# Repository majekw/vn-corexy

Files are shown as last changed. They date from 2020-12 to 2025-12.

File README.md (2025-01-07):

# vn-corexy
Very Narrow CoreXY 3D Printer

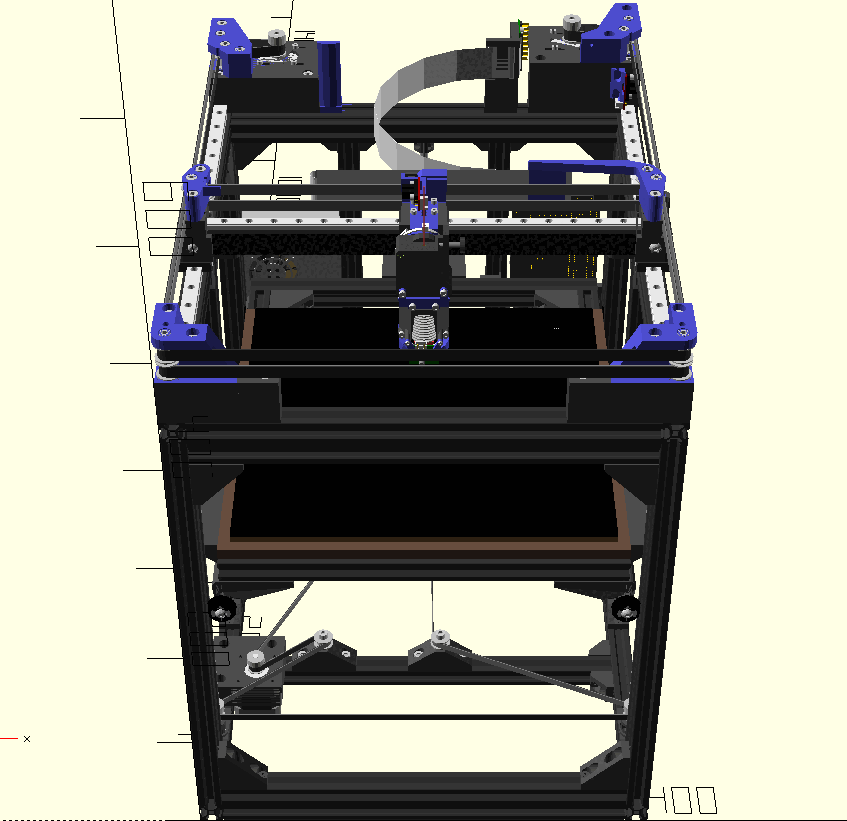
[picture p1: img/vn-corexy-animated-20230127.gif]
vn-corexy rendering


vn-corexy is designed around 300x300 mm build plate with goal to be
as compact as possible with focus on width. Current dimensions are
390(width)x520(depth)x520(height) mm. Only filament could stick above
maximum height, everything else (including cables) are within size limits.

In this repository there is OpenScad source code with 3D printer design.
There are many parameters that can be customized. In Customizer you could
choose which printed parts you want to render and save as STL file.
There are also ECHO messages in console that can be used to prepare BOM,
for example there are messages with all lengths of specific extrusion types,
GT2 belt lengts are also calculated.

**WARNING: While this is almost finished, THIS IS STILL WORK IN PROGRESS**

Forum thread (in Polish): https://reprapy.pl/viewtopic.php?f=10&t=7225

YouTube videos: https://youtube.com/playlist?list=PL_tFeFf-6be2vM2YfxNyLlgO5D3nhVPHG

# Requirements
- OpenScad https://www.openscad.org/
- NopSCADlib library https://github.com/nophead/NopSCADlib (version 21.32.0)
- for Sailfin extruder checkout Sailfin-Extruder/ git submodule
- for Moli extruder checkout Moli-Extruder/ git submodule
- for MRF extruder, download stl files from https://www.thingiverse.com/thing:5149028
  and put them into MRF/ directory

# Supported configuration
Extruders:
- TBG-Lite
- HGX Lite 2.0
Hotend:
- CHC heating block
Bed probes:
- Mini differential IR probe
- BL-Touch
Bed stabilization:
- v-slot wheels

# Known issues
- MGN12 carriage sticks 3.5mm out of frame
- bed frame could be 10mm shorter to use 4 the same wheel supports
- bed frame wheels supports are temporary, will be changed in future (work
  in progress on on MGN7 rails)
- Sailfin, Moli and MRF extruders support is not finished, BMG extruder
  is abandoned.

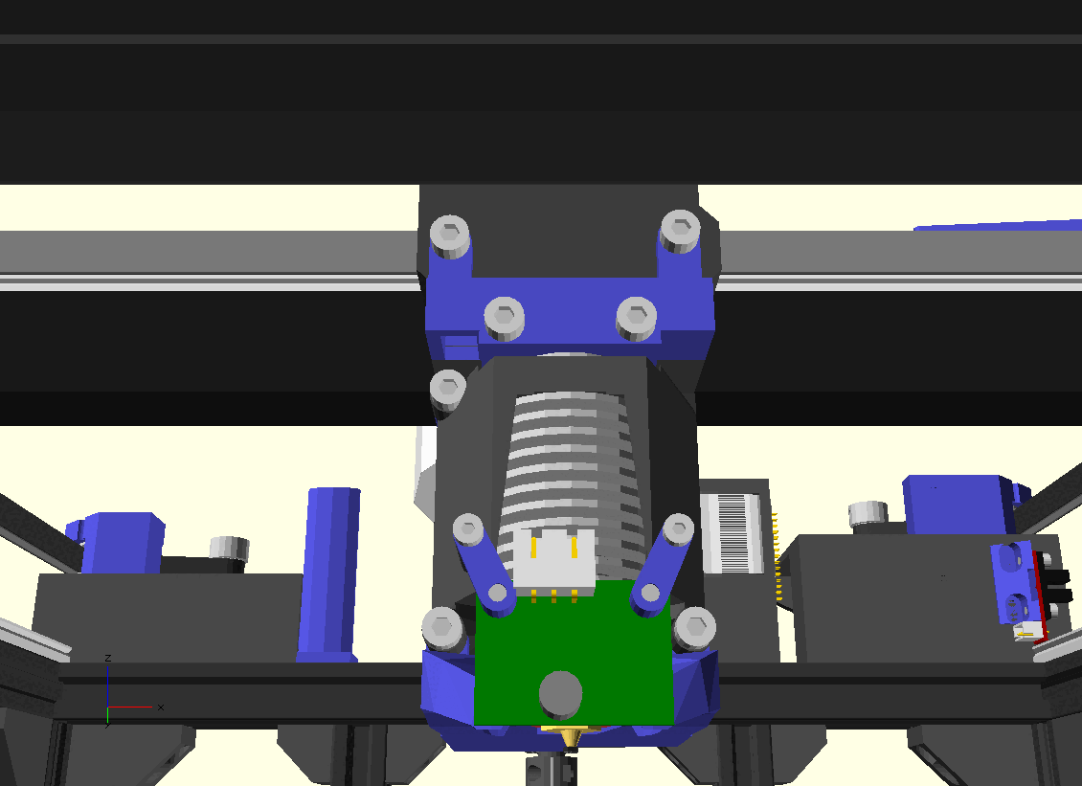
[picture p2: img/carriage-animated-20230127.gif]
vn-corexy carriage rendering


# Copyright & license
(C) 2020-2024 Marek Wodzinski <majek@w7i.pl>

This work is licensed under Creative Commons Attribution-ShareAlike 4.0 International License.
You should have received a copy of the license along with this work. 
If not, see http://creativecommons.org/licenses/by-sa/4.0/

BL-Touch model (STL) by @EA3D from: https://www.printables.com/model/301723-bltouch 
is under a Creative Commons (International License) Public Domain

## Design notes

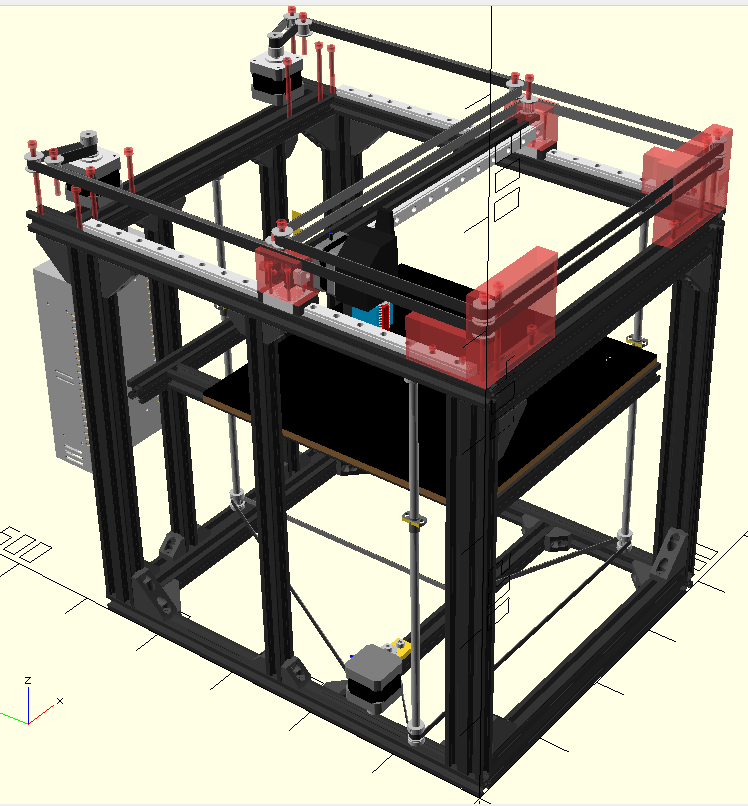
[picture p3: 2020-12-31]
img/vn-corexy-20201230.png

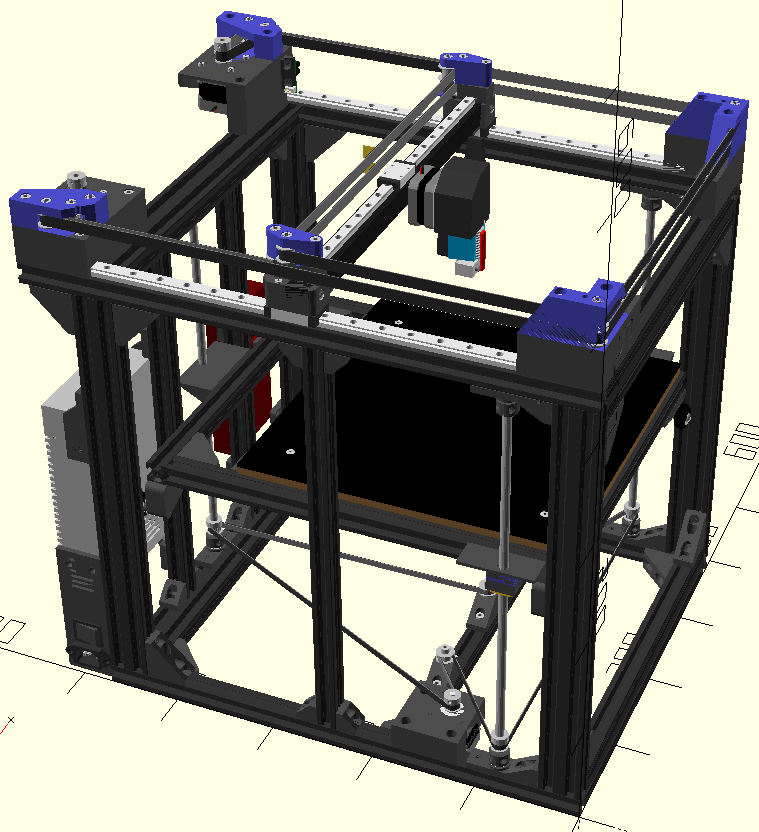
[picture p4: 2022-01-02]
img/vn-corexy-20220103.png

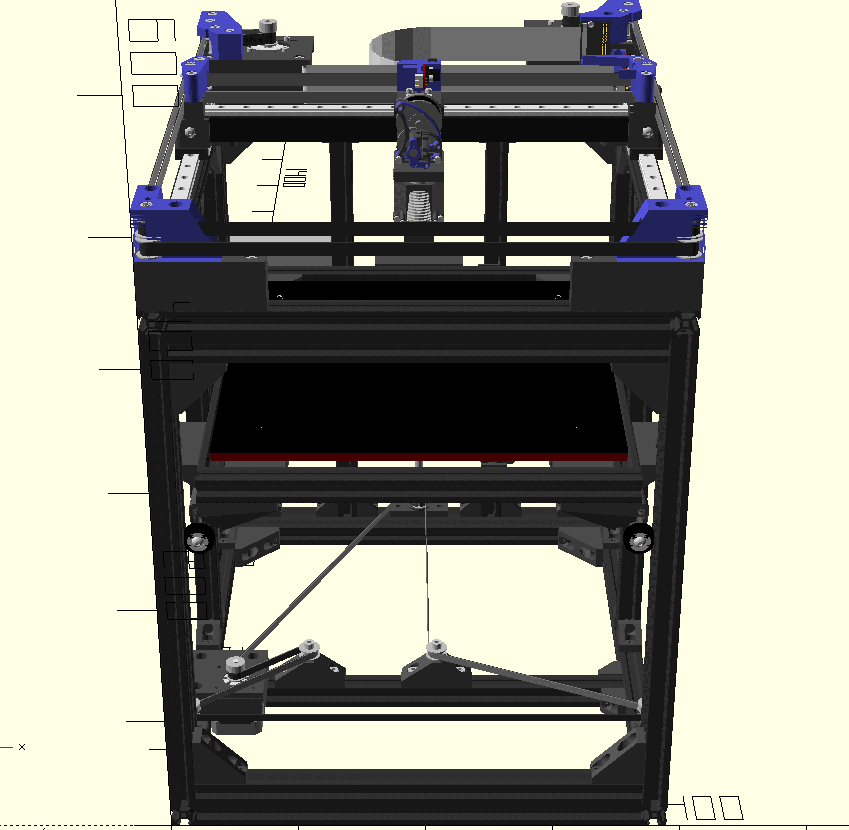
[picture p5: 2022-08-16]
img/vn-corexy-animated-20220816.gif

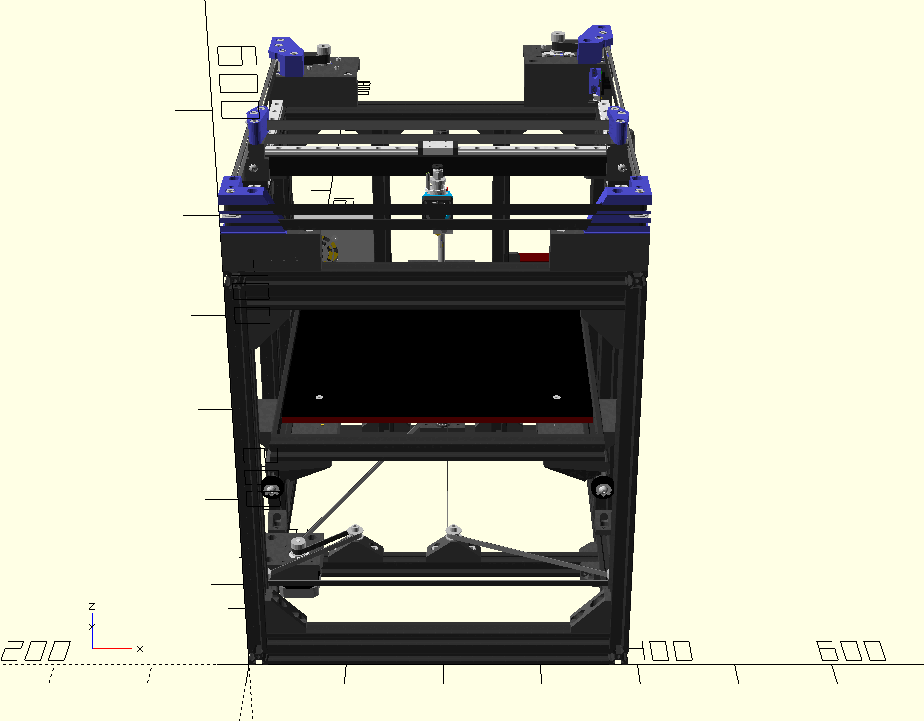
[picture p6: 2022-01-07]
img/vn-corexy-animated-20220105.gif

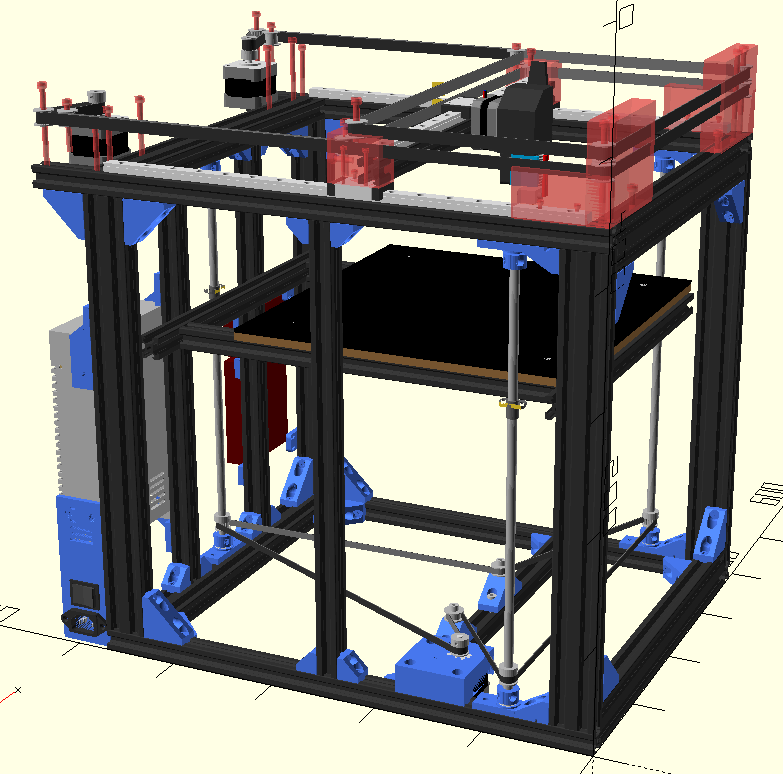
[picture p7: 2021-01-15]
img/vn-corexy-20210115.png

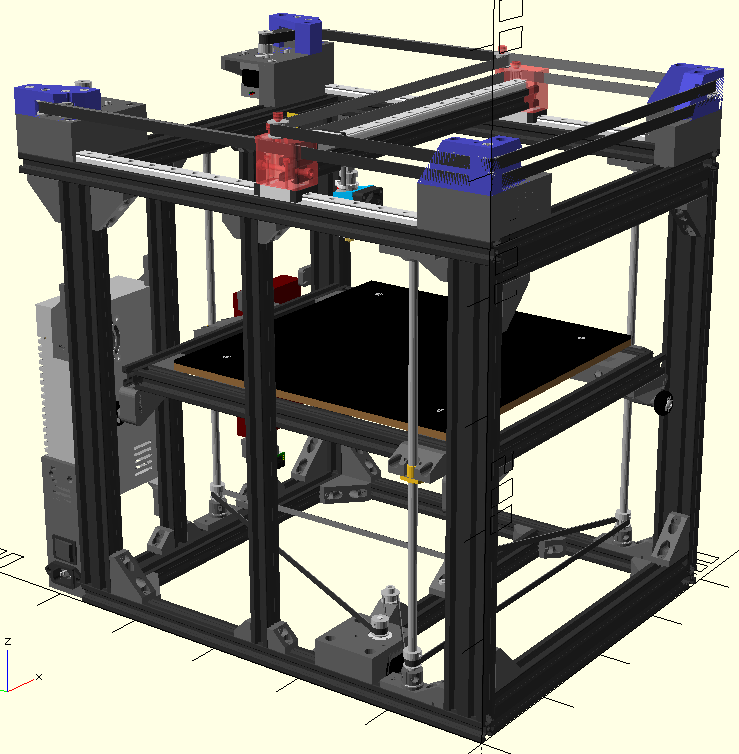
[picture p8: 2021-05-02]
img/vn-corexy-20210502.png

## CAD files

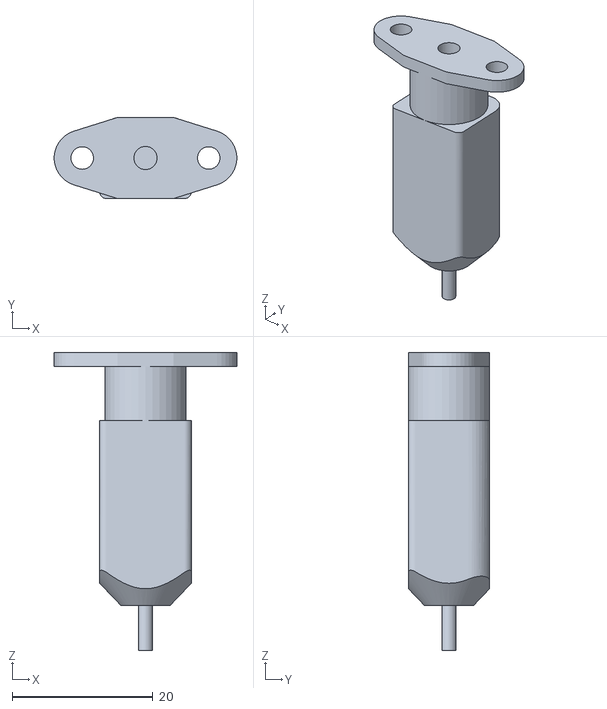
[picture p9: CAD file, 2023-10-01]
BL-touch.stl
26.0 x 11.6 x 42.4

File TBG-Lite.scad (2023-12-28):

/*
  TBG-Lite extruder OpenSCAD library
  
  Based on datasheet and measures of TBG-Lite_mockup.STEP
  (C) 2022 Marek Wodzinski <majek@w7i.pl>
  
  This library is licensed under a Creative Commons Attribution-ShareAlike 4.0 International License.
  You should have received a copy of the license along with this work.
  If not, see <http://creativecommons.org/licenses/by-sa/4.0/
  
  Some basic dimensions:
  - holes for screws: 3.2mm, head 5.5mm
  - corners: 2.5mm from edge
  - distance from front to motor plate: 21mm
  - motor center: [19.9,21.1]
  - base dimensions: 43.50mm x 22.5mm
  - filement hole from front: 8.5mm
  - back plate thickness: 4mm
*/

function TBG_w() = 43.50;
function TBG_dimensions() = [ -TBG_w()/2, // left from center
                              TBG_w()/2, // right from center
                              -8.5, // front
                              14.0 ]; // back
function TBG_holes_bottom() = [[-10.45,2,0], [8.05,4.50,0], [8.05,-4.50,0]];
function TBG_holes_left() = [[-TBG_w()/2,5.25,TBG_w()/2-10.95], [-TBG_w()/2,-2.30,TBG_w()/2+11.42]];
function TBG_holes_front() = [[-TBG_w()/2+5.00,-8.50,5.00], [15.50,-8.50,5.85], [-TBG_w()/2+3.50,-8.50,TBG_w()-3.50]];
function TBG_body() = [[-TBG_w()/2+2.5,0], [TBG_w()/2-2.5,0], [TBG_w()/2,2.5], [TBG_w()/2,10], [TBG_w()/2-8.15,18], [TBG_w()/2-8.15,TBG_w()-2.5], [TBG_w()/2-8.15-2.5,TBG_w()], [-TBG_w()/2+2.5,TBG_w()], [-TBG_w()/2,TBG_w()-2.5], [-TBG_w()/2,2.5]];
function TBG_backplate() = [[-TBG_w()/2+2.5,0], [TBG_w()/2-2.5,0], [TBG_w()/2,2.5], [TBG_w()/2,12], [TBG_w()/2-3,18], [TBG_w()/2-3,TBG_w()-2.5], [TBG_w()/2-3-2.5,TBG_w()], [-TBG_w()/2+2.5,TBG_w()], [-TBG_w()/2,TBG_w()-2.5], [-TBG_w()/2,2.5]];
function TBG_motor_position() = [[-TBG_w()/2+19.9,13,21.1],[90,-47,0]];

module TBG_lite(){
  difference(){
    union(){
      // body
      color("#404040") rotate([90,0,0]) translate([0,0,-22.50+8.50]) linear_extrude(22.50) polygon(TBG_body());
      // gear shroud
      color("#404040") translate([0,22.5-8.50-2.20,34.15]) rotate([90,0,0]) cylinder(d=26,h=7.5);
      // back plate
      color("#404040") rotate([90,0,0]) translate([0,0,-22.50+8.50]) linear_extrude(4) polygon(TBG_backplate());
      // lever
      color("#404040") translate([-TBG_w()/2+36.65,-8.5+3,0]) cube([4.50,15,55.85]);
      // screw
      translate([53.65-TBG_w()/2,-8.5+3+15/2,39.85+2]) rotate([0,-90,0]) {
        color("#404040") cylinder(h=4,d=12); // dial
        color("#808080") cylinder(h=16,d=5); // spring
        color("#a0a0a0") cylinder(h=25,d=2.85); // screw
      }
    }

    // HOLES

    // filament hole
    cylinder(h=TBG_w(),d=2); // main hole
    cylinder(h=6,d=9.6); // M10 hole
    translate([0,0,TBG_w()-3]) cylinder(h=3,d=4.2); // PTFE hole
    // bottom mount holes
    for ( i=[0:2]) {
      translate(TBG_holes_bottom()[i]) cylinder(h=4,d=3.2);
    }
    // left mount holes
    for ( i=[0:1]) {
      translate(TBG_holes_left()[i]) rotate([0,90,0]) cylinder(h=5,d=3.2);
    }
    // front mount holes
    for ( i=[0:2]) {
      translate(TBG_holes_front()[i]) rotate([-90,0,0]) {
        cylinder(h=23,d=3.2);
        cylinder(h=1.5,d=5.5);
      }
    }
    // rear motor hole
    translate([13.9,22.5-8.5,37.55]) rotate([90,0,0]) cylinder(h=4,d=3.2);
  }
}

TBG_lite();

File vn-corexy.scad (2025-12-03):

/* Very Narrow CoreXY Printer (vn-corexy)
   Created with goal: use as small space in width dimension as possible.
   (C) 2020-2024 Marek Wodzinski <majek@w7i.pl> https://majek.sh

   vn-corexy is licensed under a Creative Commons Attribution-ShareAlike 4.0 International License.
   You should have received a copy of the license along with this work.
   If not, see <http://creativecommons.org/licenses/by-sa/4.0/>
*/

/* [head position] */
pos_x=0; // [0:1:300]
pos_y=100; // [0:1:300]
pos_z=290; // [0:1:270]

/* [hotend] */
extruder_type=6; // [0:BMG extruder, 1: Sailfin extruder, 2: TBG-Lite extruder, 3: Moli extruder, 4: MRF extruder, 5: bowden, 6: HGX Lite 2.0 extruder]
hotend_type=1; // [0: standard V6, 1: V6 heatink with CHC, 2: TZT V6 ]
hotend_block_sock=true;
level_probe=1; // [0: Ormerod, 1: BL-Touch ]
bltouch_side=1; // [-1:rigt, 1:left ]

/* [printed parts] */
printed_corners=true; // [false:no, true:yes]
printed_corners_nut=1; // [0:printed nut, 1:rotating t-nut, 2:sliding t-nut]
pp_color=[0.3,0.3,0.3]; // [0:0.1:1]
pp_color2=[0.3,0.3,0.8]; // [0:0.1:1]
printed_t8_clamps=true; // [false:no, true:yes]
bed_coupler=1; // [0:permanent mount, 1:Oldham couplings]

/* [render printable parts] */
render_parts=1; // [1:T-nut M5, 2: Joint 1x1, 3: Joint 2x2, 4: PSU mounts, 5: Power socket mount, 6: Control board mounts, 7: T8 clamp, 8: T8 spacer, 9: T8 side mount, 10: T8 rear mount, 11: Front joint, 12: Z pulley support, 13: Z motor mount, 14: Cable tie mount, 15: Z pulley helper for adjusting, 16: Front Z wheel mount, 17: Rear Z wheel mount, 18: Front bed frame joint and bed support, 19: Back bed support, 20: Side bed frame to T8 mount, 21: Back bed frame to T8 mount, 22: Z endstop mount, 23: Z endstop trigger, 24: MGN12 positioning tool, 25: X motor mount base, 26: X motor mount top, 27: Y motor mount base, 28: Y motor mount top, 29: Front pulley support left down, 30: Front pulley support right down, 31: Pulley spacer 1mm, 32: Pulley spacer 2mm, 33: Front pulley support left up, 34: Front pulley support right up, 35: Oldham T8, 36: Oldham middle, 37: Oldham top sides, 38: Oldham top back, 39: Left gantry joint for CF tube, 40: Left top of gantry joint for CF tube, 41: Right gantry joint for CF tube, 42: Right top of gantry joint for CF tube, 43: MGN9 on CF positioning tool, 44: X/Y endstop trigger, 45: Y motor pulley spacer, 46: Y endstop mount, 47: CF tube M3 nut jig, 48: Extruder carriage for MGN9, 49: V6 hotend shroud, 50: Hotend blower spacer, 51: Belt lock, 52: FFC cable stopper, 53: V6 clamp, 54: Hotend mount, 55: Nema14 mount to carriage, 56: Rear carriage cable clamp, 57: FPC mount to frame, 58: TH35 mount, 59: Step down mount, 60: MOS mount, 61: Relay mount, 62: Probe mount, 63: Part cooling 1, 64: Part cooling 2, 65: Side slot front, 66: Side slot middle, 67: Side slot rear, 68: Side slot rear PS, 69: MGN7 support, 70: front MGN7 to bed connector, 71: back MGN7 to bed connector ]

/* [tweaks/hacks] */

// increase up to 1 if your printer is perfect :-), decrease when joint doesn't fit into v-slot groove
vslot_groove_scale=0.98;

// 1 for perfect printer, little larger if nut doesn't fit into hole
tnut_nut_scale=1.03;

// make holes printable without supports
bridge_support=true;
// thickness of bridge layer if bridge_support is enabled
bridge_thickness=0.20;

// use upper ball bearings for T8 rods
t8_upper_bearings=true;

// Z bed stabilization
z_bed_stab = 1; // [0: v-slot wheels, 1: MGN7 linear rails]

// correction for offset on overextrusion or slicer problems impacting on XY dimensions
printer_off=0.10; // [0:0.01:0.2]

// nozzle/path width
print_width=0.4;

// hide FPC boards and FFC cables
hide_ffc=false;

// show detailed electronic modules
show_detailed_electronics=true;

// FFC cable loop mount
ffc_loop_type=0; // [0: fin type for 80cm cable, 1: carbon rods for 60cm cable]

/* [enclosure] */
// show enclosure
show_enclosure=false;
// double sided tape thicknes
tape_thicknes=0.8;

/* [build plate] */
build_plate_w=310; // (X)
build_plate_d=310; // (Y)
build_plate_mount_space=240; // space between mounting screws

/* [build volume] */
build_x=300;
build_y=300;
build_z=290; // not used anywhere

/* [frame] */
// extrusions family size
ext=20;
// extrusion type
ext_type=1; // [0:T-SLOT, 1:V-SLOT]
// minimum margin between build plate and frame
x_margin=10;
// X gantry build type
x_gantry_type=1; // [0: V-SLOT + MGN12, 1: Carbon fiber tube + MGN9]
// CF tube size
cf_tube_size=20.20;
// CF tube wall thickness
cf_tube_wall=1.15;


// internal stuff starts here
/* [Hidden] */
include <NopSCADlib/lib.scad>
use <TBG-Lite.scad>
use <HGX-Lite2/HGX-Lite-2.scad>
use <vn-lib.scad>
eps=0.01;

// hotend variables
hotend_w=50;
hotend_d=70;
hot_y_variants=[-52,-40,-40,-40,-40,-40,-40];
hot_y=hot_y_variants[extruder_type]; // distance from gantry to nozzle
hot_z=-4;
hotend_carriage_w=36;
probe_y=(hotend_type==0) ? -19:-13; // relative to hot_y
probe_z=hot_z-49.7+1.5; // triggers 3.75mm above surface, so 1.5mm above nozzle should be ok
probe_p1=[-13,-34]; // x,z coordinates of probe mount pillars on shroud
probe_p2=[-9.25,probe_z+10.25]; // x,z coordinates of probe mount on pcb
bltouch_z=-17;
cooling_fan_z=-7.5;

// calculated
base_w=2*ext+max(build_x+hotend_w,build_plate_w+x_margin); // frame width
base_h=ext*2+400+5; //height of frame base
base_d=build_plate_d+hotend_d+2*ext+50; // frame depth
top_d=base_d+50; // top left/right profiles length, 50 is just wild guess to allow some space between X carriage and rear of frame
//y_rail_l=base_d-2*ext; // MGN rails length
y_rail_l=400;
y_rails_from_front=2.5*ext;
y_rail_carriage=MGN12H_carriage;
x_rail_carriage=MGN12H_carriage;
//x_rail_l=base_w-2*ext; // 350
x_rail_l=375;
z_pulley_support=170; //distance from front to Z pulley support
z_belt_h=48; // space from bottom of frame to Z belt
pr20=pulley_pr(GT2x20ob_pulley); // radius of puller for belt calculations
//belt_x_separation=pulley_od(GT2_10x20_toothed_idler);
belt_x_separation=6; // horizontal separation between XY belts
belt_z_separation=15; // vertical distance between XY belts
beltx_shift=34+4; // distance from frame to bottom of X belt pulley
belty_shift=beltx_shift+belt_z_separation; // distance from frame to bottom of Y belt pulley
// gantry
gantry_belt_shift=12.5; // position in Y of belt on gantry relative to center of carriage
gantry_belt_pos=gantry_belt_shift+carriage_length(y_rail_carriage)/2; // belt position relative to front of carriage
// motors
xy_motor_pos=[21+2*ext,base_d+22]; // X motor position, for Y motor is mirrored
x_motor_z=beltx_shift-5; // X motor relative Z position
y_motor_z=belty_shift-5; // Y motor relative Z position
xy_o_pulley_pos=[ext/2,base_d+ext]; // motor outer pulley position
xy_i_pulley_pos=[ext/2+belt_x_separation,base_d]; // motor inner pulley position
elec_support=135; // distance for electronic supports from edge of frame (just guess, should be adjusted for real hardware)
// extrusion joint/corner, set for M5x12
joint_screw_len=12; // length of screw
joint_screw_d=5; // screw diameter
joint_screw_head_d=8.5; // head diameter
joint_screw_washer=10; // washer diameter
joint_screw_head_h=5; // head height
joint_extr_depth=5.5; // depth of screw in extrusion profile, 6 is fine for 2020
joint_in_material=joint_screw_len-joint_extr_depth; // amount of thread in joint
joint_space=joint_screw_len-joint_extr_depth+joint_screw_head_h+joint_screw_head_d/2; // minimum space from corner to allow put two perpendicular screws
t8_frame_dist=2.5; // distance from frame to start of T8 screw
t8_bb_offset=1.5; // space from start of T8 to ball bearing
m5_hole=4.75; // hole for direct M5 screw without tapping
m3_hole=2.75; // hole for direct M3 screw without tapping
m2p5_hole=2.25; // hole for direct M2.5 screw without tapping
m2_hole=1.75; // hole for direct M2 screw without tapping
m3_insert=3.8; // hole for M3 heat insert
bed_z=base_h-2*ext-28-pos_z; // bed Z position

// Carbon fiber tube private variables
cf_above_carriage=3.5; // height of cf above carriage
cf_from_front=5; // distance from front of carriage

// oldham coupler
oldham_w=ext*1.3; // width of oldham coupler
oldham_d=ext*1.2; // depth of oldham coupler (without margin)
oldham_lh=10.5; // height of low part
oldham_mh=8; // height of middle part
oldham_margin=2.0; // space between coupler and outer shape of printer
oldham_w_h=5; // wedge height

// FPC board
fpc_z=20+31.5; // FPC connector mount Z relative to top of frame
fpc_x=base_w-42; // X position of PFC connector on Y motor
fpc30_screws=[[-4,-17.5],[-4,17.3]]; // screw positions on FPC30 board

// optical endstop holes
optical_endstop_holes=[[2.75,5.1],[2.75+19,5.1]];

// handy rails vars
MGN9_holes=[[-8,-7.5],[-8,7.5],[8,-7.5],[8,7.5]];
MGN7_holes=[[-6.5,-6],[-6.5,6],[6.5,6],[6.5,-6]];
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

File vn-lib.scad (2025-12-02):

/*
   Basic shapes library: vn-lib.scad
   (C) 2023 Marek Wodzinski <majek@w7i.pl> https://majek.sh

   This library is licensed under a Creative Commons
   Attribution-ShareAlike 4.0 International License.
   You should have received a copy of the license along with this work.
   If not, see <http://creativecommons.org/licenses/by-sa/4.0/>
*/

/* diamond
  dim - [x,y,z]
  dim.x - width of diamond
  dim.y - height of diamond
  dim.z - thickness of extruded diamond
*/
module diamond(dim){
  linear_extrude(dim.z) polygon([ [0,dim.y/2], [dim.x/2,0], [dim.x,dim.y/2], [dim.x/2,dim.y] ]);
}

/*
  extruded square triangle
  a - side size
  h - height/lenght of element
*/
module triangle(a,h){
  translate([0,0,-h/2]) linear_extrude(h) polygon([[0,0], [a,0], [0,a]]);
}

/*
  extruded square triangle
  a,b - sides
  h - height/lenght of element
*/
module triangle2(a,b,h){
  translate([0,0,-h/2]) linear_extrude(h) polygon([[0,0], [a,0], [0,b]]);
}

/* cube minus quarter of cylinder
  r - size of rectangle
  h - height/lenght of element
  eps - offset for difference to look nice in preview (default=0.01)
*/
module round_corner(r,h,eps=0.01){
  difference(){
    cube([r,r,h]);
    translate([r,r,-eps]) cylinder(r=r,h=h+2*eps);
  }
}

/* hull between 2 cylinders
  d - diameter of cylinders
  h - height of cylinders
  l - space between centers of cylinders
*/
module slot(d,h,l){
  hull(){
    cylinder(d=d,h=h);
    translate([l,0,0]) cylinder(d=d,h=h);
  }
}

/* 'extrude' along path
   parameters - [ step_definition, step_definition, ... ], eps
   step_definition - [ translation, rotation, shape ]
   translation - argument to translate()
   rotation - argument to rotate()
   shape - argument to polygon()
   eps - height of extrude of shape (default=0.01)
*/
module path_extrude(trs,offset=0,eps=0.01){
  for (cc=[0:len(trs)-2]) {
    hull(){
      translate(trs[cc][0]) rotate(trs[cc][1]) linear_extrude(eps) offset(delta=offset) polygon(trs[cc][2]);
      translate(trs[cc+1][0]) rotate(trs[cc+1][1]) linear_extrude(eps) offset(delta=offset) polygon(trs[cc+1][2]);
    }
  }
}

/* return points of square
*/
function square_points(x,y) = [[0,0],[x,0],[x,y],[0,y]];

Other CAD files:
HGX-Lite2/HGX-Lite-2.scad

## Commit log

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2020-12-28 Separate preview and render parts.
    [vn-corexy.scad]
2020-12-29 Customize printable corners, lower details for preview.
    [vn-corexy.scad]
2020-12-29 Fix joiner hole for rotating t-nut, lot of comments.
    [vn-corexy.scad]
2020-12-30 Expose tweaks to Customizer.
    [vn-corexy.scad]
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2020-12-31 Make BMG extruder more visible.
    [vn-corexy.scad]
2021-01-08 Frame correction, scale for printed holes, lower belts by 10mm.
    [vn-corexy.scad]
2021-01-09 Add PSU mounts and control board.
    [vn-corexy.scad]
2021-01-09 Add power socket and switch mount.
    [vn-corexy.scad]
2021-01-10 Added control boaard mounts, improved power socket and PSU mounts.
    [vn-corexy.scad]
2021-01-12 Rotate and move Z motor, adjust all pulleys and belt.
    [vn-corexy.scad]
2021-01-13 Add Z rod clamps and spacers.
    [vn-corexy.scad]
2021-01-13 Add support for ball bearings/Z rods.
    [vn-corexy.scad]
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2021-01-14 Allow to customize printable parts color.
    [vn-corexy.scad]
2021-01-14 Add Z pulley support.
    [vn-corexy.scad]
2021-01-15 Fix Z pulley support, add Z motor mount and cable mounts.
    [vn-corexy.scad]
2021-01-19 Echo calculated rails length, but use standard in project.
    [vn-corexy.scad]
2021-01-31 Refactored T8 screw parts, added metal clamp, comments.
    [vn-corexy.scad]
2021-01-31 T8 brass nut reworked.
    [vn-corexy.scad]
2021-02-08 Add T8 pulley adjistment helper, start to redesign of Z bed.
    [vn-corexy.scad]
2021-02-09 Fix linear rails after breaking changes in NopSCADlib, add v-wheel.
    [vn-corexy.scad]
2021-02-09 Add front wheels mounts for Z, add small v-slot wheel, rename one module.
    [vn-corexy.scad]
2021-02-11 More work with Z bed.
    [vn-corexy.scad]
2021-02-11 Move bed to separate module.
    [vn-corexy.scad]
2021-02-12 Some tweaks to gantry/head.
    [vn-corexy.scad]
2021-02-12 Redesign build plate mount.
    [vn-corexy.scad]
2021-02-12 Add front bed joiners.
    [vn-corexy.scad]
2021-02-12 Add back bed support.
    [vn-corexy.scad]
2021-02-13 Mount bed frame to T8 screws, bed supports rounded.
    [vn-corexy.scad]
2021-02-13 Make joiner_bed printable again.
    [vn-corexy.scad]
2021-02-13 Make bed support more printable.
    [vn-corexy.scad]
2021-02-13 More print fixes.
    [vn-corexy.scad]
2021-02-14 Add Z end-stop, corrections in bed to T8 joiner.
    [vn-corexy.scad]
2021-02-19 Add linear rail mount tool, Z endstop position correction.
    [vn-corexy.scad]
2021-02-21 Some work on gantry.
    [vn-corexy.scad]
2021-02-21 Replace some hack/scales with printer offset.
    [vn-corexy.scad]
2021-04-01 Add logo, some work on XY belts/motors mounts.
    [vn-corexy.scad]
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2021-04-02 Rework bridging in upside down holes.
    [vn-corexy.scad]
2021-04-02 Move motors/pulleys coordinates to global variables, make X motor mount printable using customizer.
    [vn-corexy.scad]
2021-04-03 Fixes in X motor mount, add second color.
    [vn-corexy.scad]
2021-04-03 Add Y motor mount.
    [vn-corexy.scad]
2021-04-05 Move Y motor 2mm up.
    [vn-corexy.scad]
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2021-05-02 Lower part of front pulleys support.
    [vn-corexy.scad]
2021-05-02 Upper front pulley mount.
    [vn-corexy.scad]
2021-05-02 Small fixes to front pulley mount.
    [vn-corexy.scad]
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2021-05-05 Adapt X axis to carbon fiber tube+MGN9.
    [vn-corexy.scad]
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2022-01-01 Some work on left gantry joiner for CF tube.
    [vn-corexy.scad]
2022-01-01 Refactoring Y position of belt and pulleys on gantry.
    [vn-corexy.scad]
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2022-01-01 Move oldham and cf variables to top of file.
    [vn-corexy.scad]
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2022-01-02 Small fix to left gantry joiner, start working on right side.
    [vn-corexy.scad]
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2022-01-02 Gantry joiners fixes.
    [vn-corexy.scad]
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2022-01-02 Redesign Y motor mount, add Y end stop.
    [vn-corexy.scad]
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2022-01-03 Fix hole diameter for top screw in gantry joiner.
    [vn-corexy.scad]
2022-01-04 Fix printability of top gantry joints.
    [vn-corexy.scad]
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2022-01-04 Fix Y end stop mount.
    [vn-corexy.scad]
2022-01-04 Jig for placing M3 nuts inside CF tube.
    [vn-corexy.scad]
2022-01-05 Remove rendering of all parts, add used version of NopSCADlib to README.
    [vn-corexy.scad]
2022-01-07 Animated gif, beginning of X carriage and hotend.
    [vn-corexy.scad]
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2022-01-09 Update last animation, better coordinates for generating animation.
    [vn-corexy.scad]
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2022-01-19 Some work on hotend, make front top corners round.
    [vn-corexy.scad]
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2022-01-29 Corrections to hotend air guide.
    [vn-corexy.scad]
2022-01-30 Rotate pins on Omerod, start work on hotend mount.
    [vn-corexy.scad]
2022-01-31 Added MRF extruder, more work on hotend carriage.
    [vn-corexy.scad]
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2022-02-02 Enlarge rear part of Sailfin, move motor, update color of end-stop sensor.
    [vn-corexy.scad]
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2022-08-14 Allow hiding FFC cables and FPC board on preview.
    [vn-corexy.scad]
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2022-10-04 Pancake 23mm motor fix, add option to render without extruder (bowden).
    [vn-corexy.scad]
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2022-10-08 Mount for Sailfin, corrections to hotend mount.
    [vn-corexy.scad]
2022-10-25 Make nema14 customizable, origin is top of front plate.
    [vn-corexy.scad]
2022-10-31 Move bottom carriage plate and part cooling fans up 4mm.
    [vn-corexy.scad]
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2022-11-04 Redesign of MGN9 carriage.
    [vn-corexy.scad]
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2022-11-06 Small corrections to MGN9 carriage and TBG mount.
    [vn-corexy.scad]
2022-11-06 Nema14 mount to carriage, add cables input to motor.
    [vn-corexy.scad]
2022-11-08 Improvements to MGN9 carriage + rear cable lock.
    [vn-corexy.scad]
2022-11-10 Change rear of carriage: cable and belt mounts.
    [vn-corexy.scad]
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2022-11-30 Rework of FFC cable.
    [vn-corexy.scad]
2022-12-02 More work on FFC cable - change of frame mount point.
    [vn-corexy.scad]
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2022-12-03 Add TH35 rail and mounting, update SKR mount.
    [vn-corexy.scad]
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2022-12-05 Add real look of MOS and relay modules.
    [vn-corexy.scad]
2022-12-06 Allow disabling detailed rendering of electronics - saves 25% on rendering time.
    [vn-corexy.scad]
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2022-12-11 Fix lower part of carriage.
    [vn-corexy.scad]
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2022-12-29 Correction to hotend heatink shroud.
    [vn-corexy.scad]
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2023-01-01 Update probe coordinates, TBG-Lite fix crash into frame.
    [vn-corexy.scad]
2023-01-02 Fix TBG fix, move FFC fin toward center.
    [TBG-Lite.scad, vn-corexy.scad]
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2023-01-03 Move cooling fans and X endstop to carriage module.
    [vn-corexy.scad]
2023-01-03 Update required version of NopSCADlib, update year in (C).
    [vn-corexy.scad]
2023-01-04 Add rear TBG mount, updates to cable holes in hotend mount.
    [vn-corexy.scad]
2023-01-06 Rework cable paths and reinforce hotend mount.
    [vn-corexy.scad]
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2023-01-12 Parameterize cooling fan Z position, start working on fan outlets.
    [vn-corexy.scad]
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2023-01-21 Improve air flow on right fan, update blower definitions.
    [vn-corexy.scad]
2023-01-24 Move basic modules to vn-lib library, add path_extrude to library.
    [vn-corexy.scad, vn-lib.scad]
2023-01-26 Add offset to path_extrude, add square_points function to library.
    [vn-lib.scad]
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2023-01-26 Corrections to fan duct, updated variables for animations.
    [vn-corexy.scad]
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2023-03-25 Add Orange PI Zero 2, remove one fan.
    [vn-corexy.scad]
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2023-12-31 Motor angle correction for HGX.
    [HGX-Lite-2.scad]
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2024-01-10 Start work on bed stabilization with linear rails.
    [vn-corexy.scad]
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2024-11-21 Shorter MGN7 rails for bed stabilization.
    [vn-corexy.scad]
2025-01-07 Add MGN7 rails for bed stabilization, use BL-Touch as default, add limits for axis in customizer.
    [vn-corexy.scad]
2025-01-10 MGN7 position correction
    [vn-corexy.scad]
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
